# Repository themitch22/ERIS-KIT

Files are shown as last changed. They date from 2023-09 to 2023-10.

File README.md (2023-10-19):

ERIS KIT Delta 3D Printer
=========================

ERIS PARTS ONLY KITS

Manufactured in Sept & Oct 2023. 

MITCH3D inspired the kit version.  Many folks on social media have seen the great work Mitch has done with SeeMeCNC printers.  The kit is a community project.  As such, SeeMeCNC only warranties the parts included. 

The factory ERIS KIT does not include a hotend or control board.  The controller and any other electronic parts will need to be sourced seperately.

More information to complete your printer found here:
www.mitch3d.com/eris

####

Team SeeMeCNC (:

Open Source

=========================

I will maintain this fork with additional upgrade parts for the Eris Parts Kit and additional documentation.

Recommended Upgrade BOM:
*  E3D Revo Micro 12V kit
*  BTT SKR Mini E3 V3 control board
*  Voron V0.2 Mini OLED Display Controller (designed by Timmit99)
*  2 x GDSTime 3010 12V Blower Fans
*  8 x M2 x 10mm self-tapping screws
*  8 x M3 x 8mm BHCS
*  Various JST-XH crimp connectors
*  Various Dupont crimp connectors

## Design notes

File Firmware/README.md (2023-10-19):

ERIS KIT Delta 3D Printer
=========================

Firmware setup found at mitch3d.com/eris

####

Team SeeMeCNC (:

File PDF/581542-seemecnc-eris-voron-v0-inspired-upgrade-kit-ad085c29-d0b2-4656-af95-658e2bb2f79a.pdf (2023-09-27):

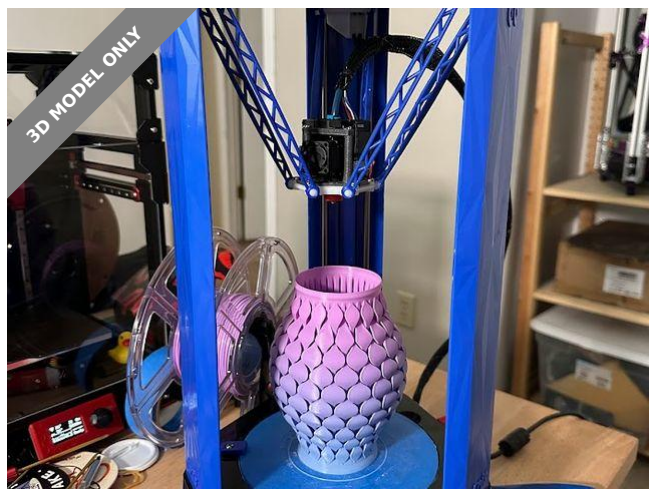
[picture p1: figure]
3D MODEL ONLY

### Summary

The ultimate upgrade package for your SeeMeCNC Eris mini delta printer (2016)

3D Printers (https://printables.com/model?categoryId=1) > Other Printer Parts & Upgrades (https://printables.com/model?categoryId=2)

Tags: raspberry | pi | eris | klipper | voron | seemecnc | v0

The SeeMeCNC Eris, (https://www.seemecnc.com/products/eris-desktop-3d-printer) released in 2016, was a ready to print out of the box mini delta printer made with injection molded parts and custom extruder hotend parts almost entirely US-made. They even sold these printers at retail stores like Microcenter!

I loved this printer, but it had some major issues:

The ATMEGA2560 based Rambo Mini board with Repetier limits a delta printers speed and precision
The HE280 based PCB on the effector used an accelerometer to detect nozzle probes for auto-calibration. It was a very advanced idea for 2016, but with modern firmware, delta-calibration techniques are way more reliable. For this mod, I have stuck with Manual Delta Calibration in Klipper and it's been super reliable for first layers.
The stock hotend and single 3010 fan was lacking. It used a bowden tube to a steel heatbreak (partially all metal) that attached the hotend to the effector PCB, the heater cartridge was a power resistor

Mitch 3D (https://printables.com/@Mitch3D)

### SeeMeCNC Eris

### Voron V0-Inspired

### Upgrade Kit

VIEW IN BROWSER (https://printables.com/model/581542-seemecnc-eris-voron-v0-inspired-upgrade-kit)

updated 13. 9. 2023 | published 13. 9. 2023

•

•

•

(about 20W), the single 3010 fan sucked air past the heatsync and it was also the part cooling with a shroud. The original print head did not have adequate heating and cooling.
The Eris had no LCD controller. It had a light up logo on front which I think was supposed to be an addressable LED, but all the control was done through MatterControl (https://www.matterhackers.com/store/l/mattercontrol/sk/MKZGTDW6) (Matterhackers) so it wasn't really portable without a PC attached.

Parts Needed and Instructions (links to vendors and files)

Original SeeMeCNC Eris - I have not found these on ebay but there are a few still floating around or collecting dust on a shelf.
BTT SKR Mini E3 V3 control board (https://biqu.equipment/products/bigtreetech-skr-mini-e3-v2-0-32-bit-control-board-for-ender-3) - It's about the same footprint as the Rambo Mini but has way more power and IO. A SKR Pico would work as well but the connectors are on the edge which might interfere with the case. You will also want an external microSD connector (https://a.co/d/5BjRwnt) pass through one of the holes and stuck to the outside of the case, this helps flash board firmware from Klipper.
SKR Mini Mounting Bracket (https://www.printables.com/model/172510-bigtreetech-skr-mini-e3-v2030-bracket) - by w0nd4bra (https://www.printables.com/@w0nd4bra) this bracket barely fits where the Rambo Mini use to slot in. I checked for clearance and marked and drilled two holes for M3x8 screws and used heat set inserts to fasten it to the shelf. You might want to use VHB tape instead. It will interfere with the corner screw bosses, you might have to sand that away. See the pictures for how I mounted it.
Raspberry Pi 3B or equivalent - These are still hard to get, you can also use the BTT Pi V1.2, the mount I designed will fit standard a Pi 3/4B, you will need to glue and heat insert the standoffs. It clips into the frame of the LCD mount backside. It provides a pass-through hole for the USB cable.
Voron V0.2 Mini OLED Display Controller (https://west3d.com/products/v0-display) (designed by Timmit99)- This controller works with Klipper with a short USB cable to the Pi (I cut the micro USB side and soldered it to a dupont connector). You will need to print the Voron V0.2 display faceplate, knob, and diffuser (https://github.com/VoronDesign/Voron-0/tree/Voron0.2r1/STLs/Display) (or hotglue like I used) using M2x10 self-tapping screws to mount into my custom Eris LCD mount. The LCD mount should slot right into the base like the original Eris logo.
E3D Revo Micro 12V kit (https://e3d-online.com/products/revo-micro) - The Revo was the smallest, lightest, easiest hotend for the Eris. The top and base mount with M3x8 screws into the plastic. The Revo wires slip through the back side cut out. I initially worked with Hotends.com to come up with a custom mount for their J-head Farmer hotend (https://hotends.com/printer-parts/hotends/j-head-farmer-hotend/) but it was too heavy. The E3D Revo comes with a 5V fan which needs a step-down converter I just soldered into the existing whip fan connections. The current design

you will need to sand down the fan shroud to not interfere

with the 3010 blowers (see picture). I would also highly
recommend using capricorn XS tube to reduce the long bowden

•

•

•

•

•

•

•

### Model files

issues like retraction, I can get away with 4mm retractions with this setup. Also check if you have the original EZstruder, you really want the latest SeeMeCNC EZR extruder (https://www.seemecnc.com/products/ezrstruder) it honestly works great as is. GDSTime 3010 12V Blower Fans (https://a.co/d/asESusC) - These part cooling fans really make a huge difference in the performance of the Eris. My effector mount base and top has M2 x 10 screw points for mounting them and a duct that blows down on to the part (I found no need for a nozzle)
I used the existing whip but removed the original connectors and soldered them to a 8-pin GX16 connector (https://a.co/d/5zVXuh1) (Use this guide for wiring) (https://hotends.com/kb/eris-3d-printer/) mounted to a hole I drilled in the case, I soldered and crimped the other side of the whip to the components on the effector side. This allows you to easily remove the whole assembly for troubleshooting and travel. You will need JST-XH crimps connectors (https://a.co/d/ebk87RT) for the BTT board and maybe some dupont 2.54 pitch connectors and crimpers.

Basically if you've build a Voron V0.1/0.2 you can handle this mod. It is basically a Voron V0 delta but not nearly as rigid or fast.

Please comment or message me and I will publish the Klipper config files needed for the Eris.
The printing results are incredible considering the age and plastic shell of this delta. It is limited to 500mm/s2 accels and 125mm/s rapids, which is quite slow for modern standards but you can't beat the portability and looks of this little printer.

If you have an Eris and want to do this mod, please message me I will try to help you with whatever I can. STEP files included if you need to modify something, I can provide Fusion 360 files if needed (they're too messy to publish).

•

•

eris-lcd-mount-pi-attachment-standoff.3mf

eris-revo-3010-effector-mount-top.3mf

### License

This work is licensed under a
Creative Commons (4.0 International License)

Attribution (http://creativecommons.org/licenses/by/4.0/)

✖ | Sharing without ATTRIBUTION
✔ | Remix Culture allowed
✔ | Commercial Use
✔ | Free Cultural Works
✔ | Meets Open Definition

eris-mini-lcd-mount.3mf

eris-lcd-mount-pi-attachment.step

eris-revo-3010-effector-mount-base.3mf

eris-mini-lcd-mount-v5.step

eris-revo-3010-effector-mount.step

eris-lcd-mount-pi-attachment-body.3mf

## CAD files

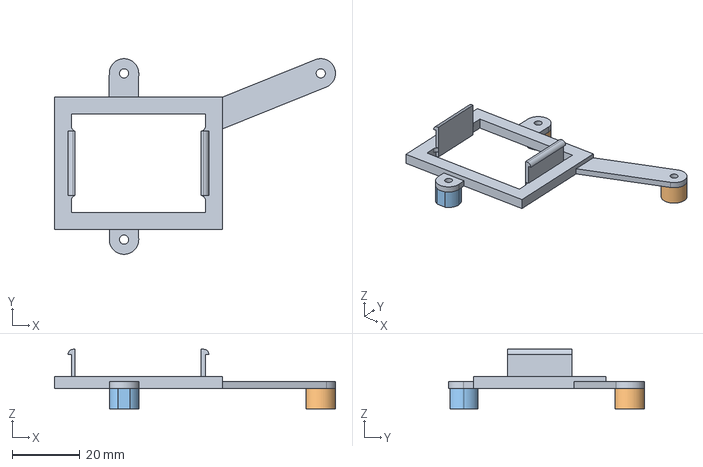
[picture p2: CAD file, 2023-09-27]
CAD/Eris LCD Mount Pi Attachment.step
82.8 x 57.7 x 17.6 mm

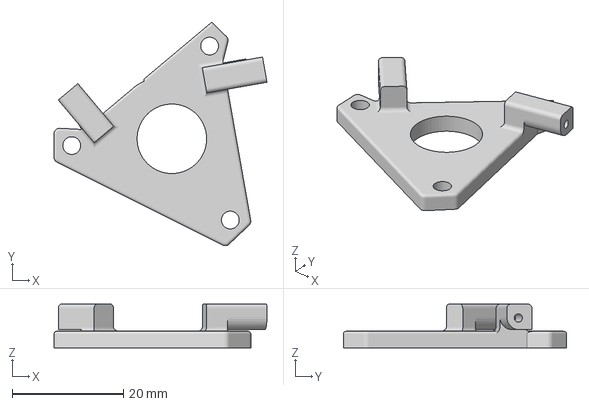
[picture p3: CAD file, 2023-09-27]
STL/Eris Revo 3010 Effector Mount Top.3mf
38.3 x 40.2 x 7.87 mm

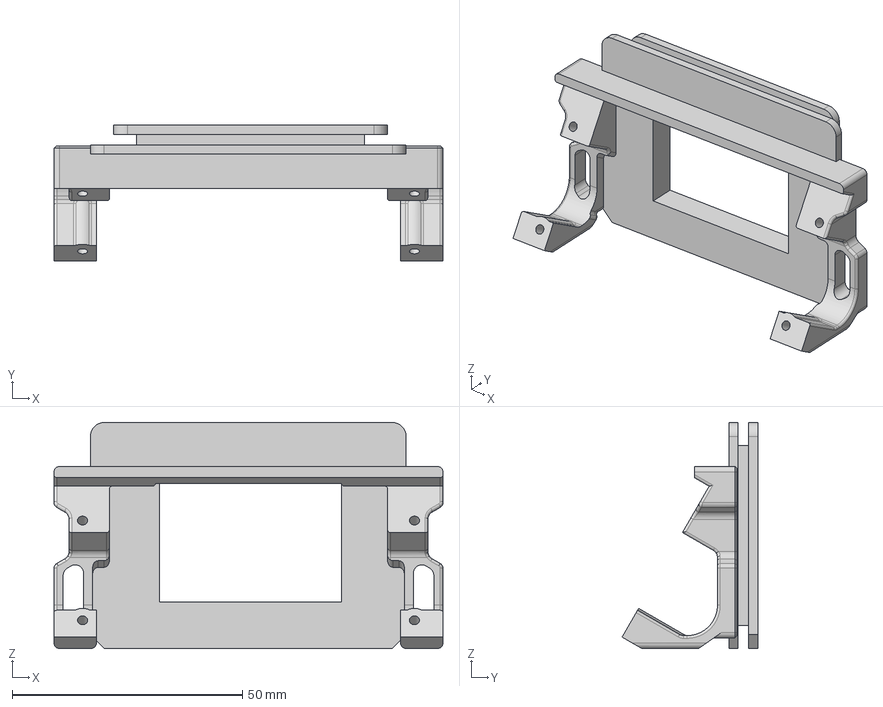
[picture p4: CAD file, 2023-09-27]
CAD/Eris Mini LCD mount v5.step
84.4 x 29.5 x 49.0 mm
Display Left Foot
Display Right Foot

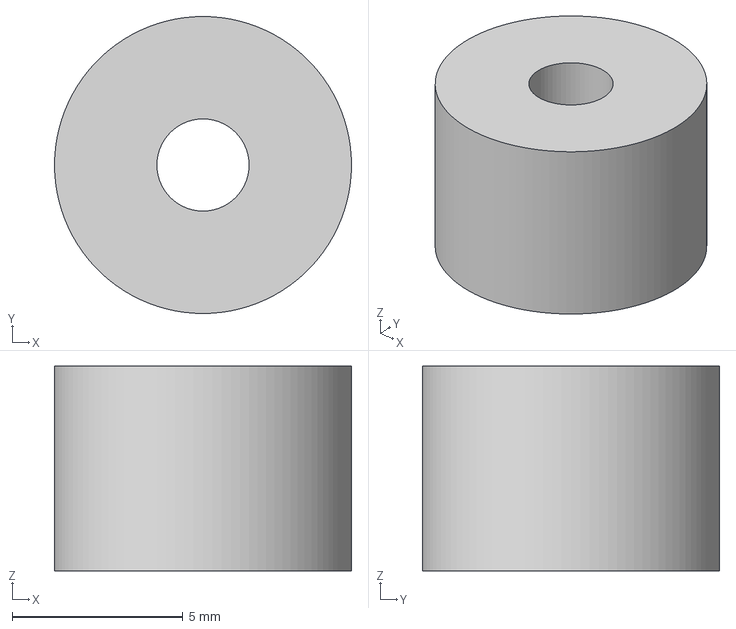
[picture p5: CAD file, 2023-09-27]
STL/Eris LCD Mount Pi Attachment Standoff.3mf
8.70 x 8.70 x 6.00 mm

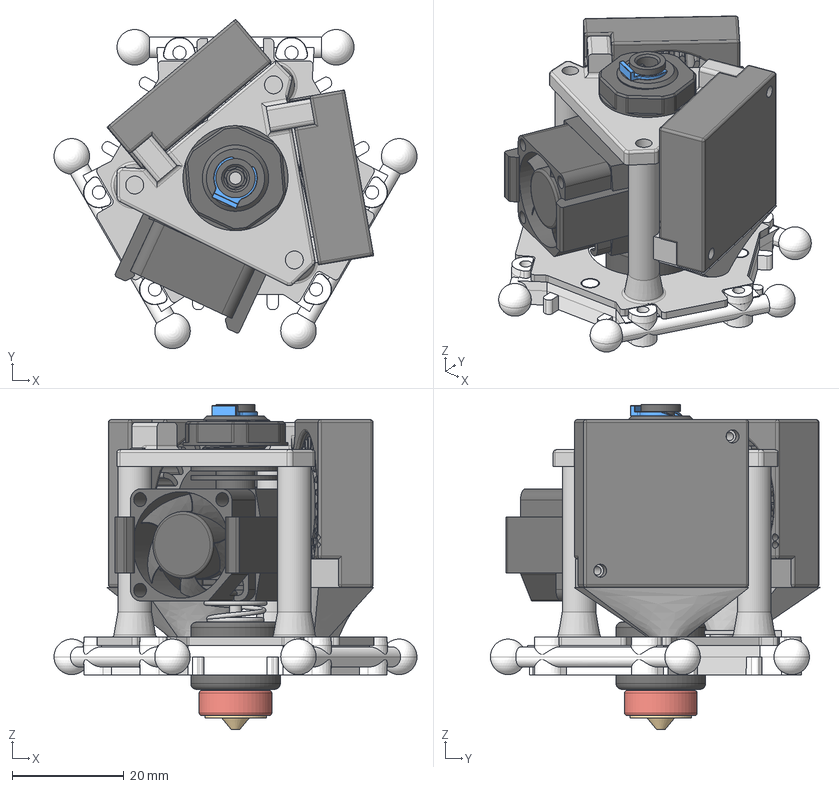
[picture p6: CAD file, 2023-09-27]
CAD/Eris Revo 3010 Effector Mount.step
64.8 x 58.8 x 58.1 mm
71200 HE280 Assembly_86005 Platform
71200 HE280 Assembly_Blower 30mm x 30mm x 10mm x 2
Heatblock
Nozzle
Threaded_Nut
Spring
Heatbreak
Heatsink
Cable_Exit
Coupling_Clip
20x20x10_Fan
Fan_Mount
Coupling

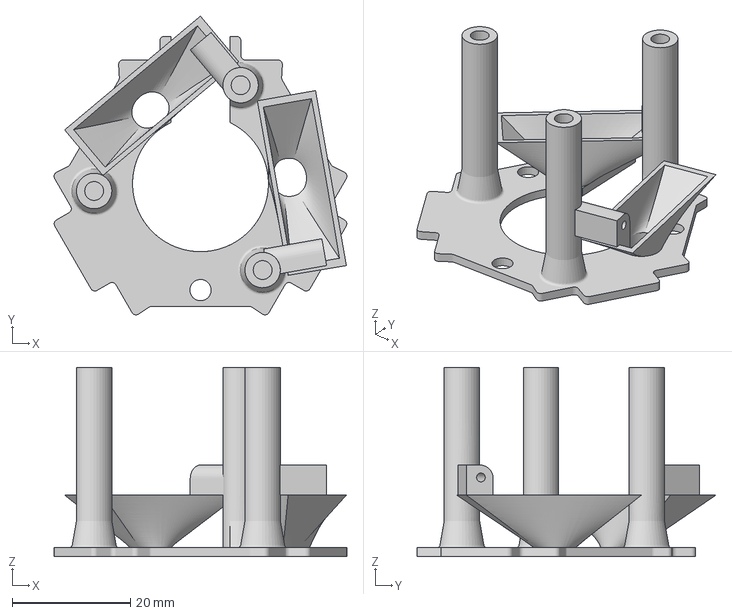
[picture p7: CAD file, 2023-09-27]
STL/Eris Revo 3010 Effector Mount Base.3mf
49.6 x 50.6 x 32.0 mm

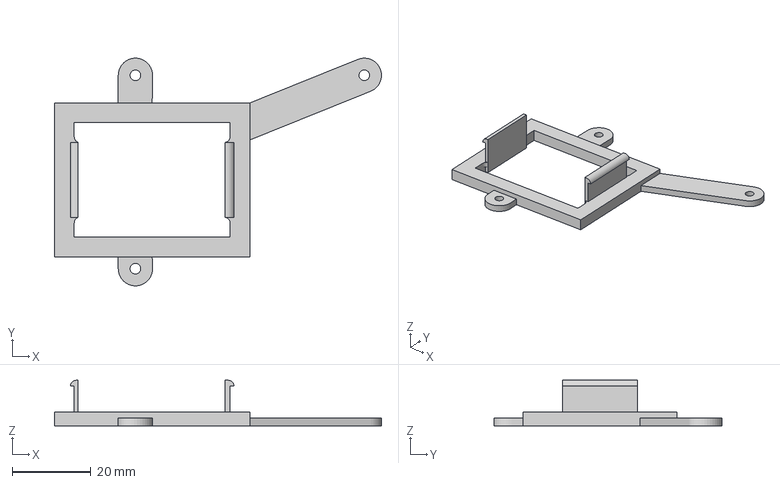
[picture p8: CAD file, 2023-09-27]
STL/Eris LCD Mount Pi Attachment Body.3mf
82.8 x 57.7 x 11.6 mm

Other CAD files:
STL/Eris Mini LCD Mount.3mf
CAD/Eris LCD Mount Pi Attachment v2.f3d
CAD/Eris Mini LCD mount v5 v1.f3d
CAD/Eris Revo Update Effector v15.f3z

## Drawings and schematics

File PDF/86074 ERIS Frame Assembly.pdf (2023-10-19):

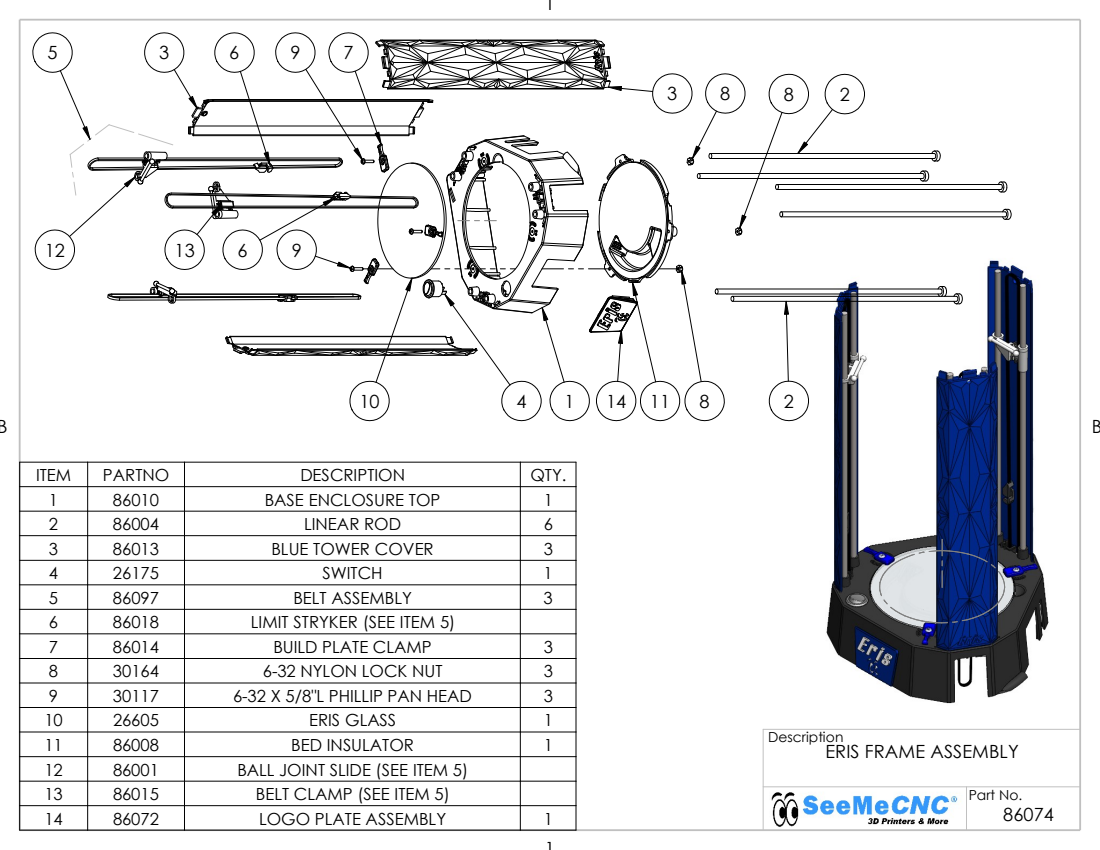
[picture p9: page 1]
BED INSULATOR

ITEM | PARTNO | DESCRIPTION | QTY.
1 | 86010 | BASE ENCLOSURE TOP | 1
2 | 86004 | LINEAR ROD | 6
3 | 86013 | BLUE TOWER COVER | 3
4 | 26175 | SWITCH | 1
5 | 86097 | BELT ASSEMBLY | 3
6 | 86018 | LIMIT STRYKER (SEE ITEM 5)
7 | 86014 | BUILD PLATE CLAMP | 3
8 | 30164 | 6-32 NYLON LOCK NUT | 3
9 | 30117 | 6-32 X 5/8"L PHILLIP PAN HEAD | 3
10 | 26605 | ERIS GLASS | 1

Description
ERIS FRAME ASSEMBLY

12 | 86001 | BALL JOINT SLIDE (SEE ITEM 5)
13 | 86015 | BELT CLAMP (SEE ITEM 5)
14 | 86072 | LOGO PLATE ASSEMBLY | 1

Part No. 86074

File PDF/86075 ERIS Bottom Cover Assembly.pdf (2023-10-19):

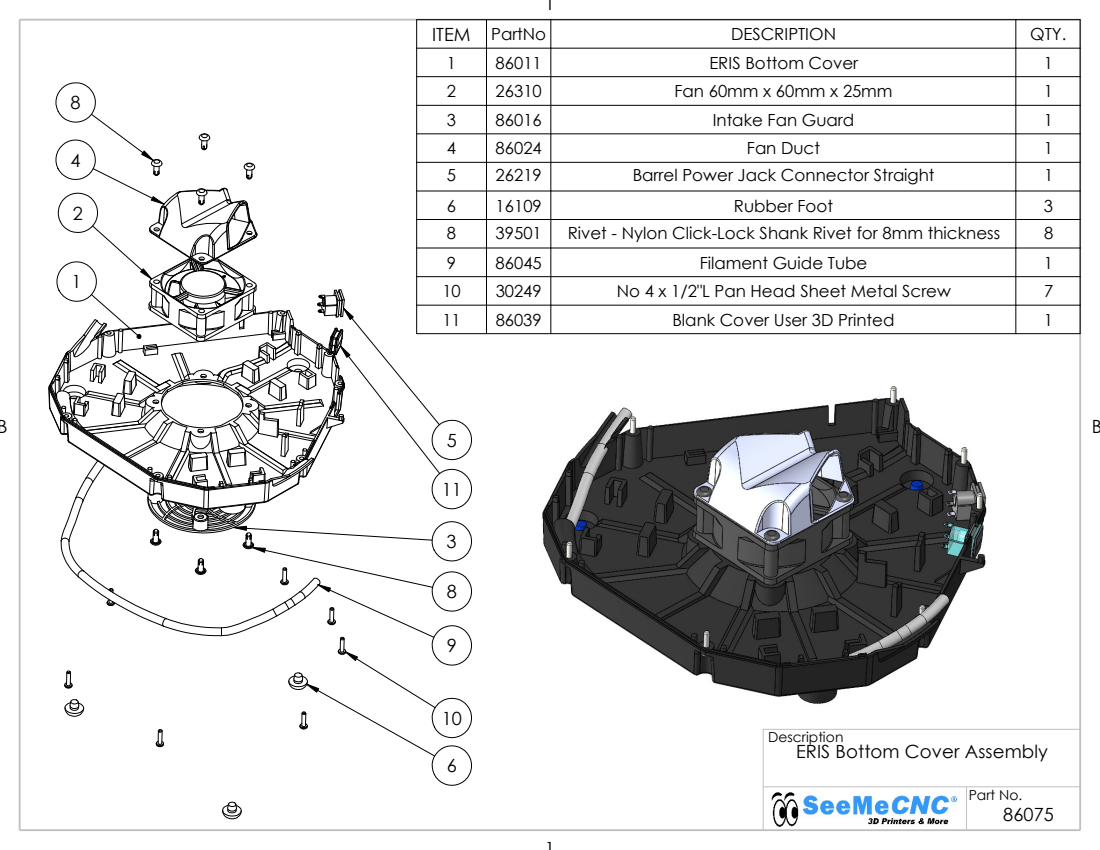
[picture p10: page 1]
Part No.

ITEM | PartNo | DESCRIPTION | QTY.
1 | 86011 | ERIS Bottom Cover | 1
2 | 26310 | Fan 60mm x 60mm x 25mm | 1
3 | 86016 | Intake Fan Guard | 1
4 | 86024 | Fan Duct | 1
5 | 26219 | Barrel Power Jack Connector Straight | 1
6 | 16109 | Rubber Foot | 3
8 | 39501 | Rivet - Nylon Click-Lock Shank Rivet for 8mm thickness | 8
9 | 86045 | Filament Guide Tube | 1
10 | 30249 | No 4 x 1/2"L Pan Head Sheet Metal Screw | 7
11 | 86039 | Blank Cover User 3D Printed | 1

Description
ERIS Bottom Cover Assembly

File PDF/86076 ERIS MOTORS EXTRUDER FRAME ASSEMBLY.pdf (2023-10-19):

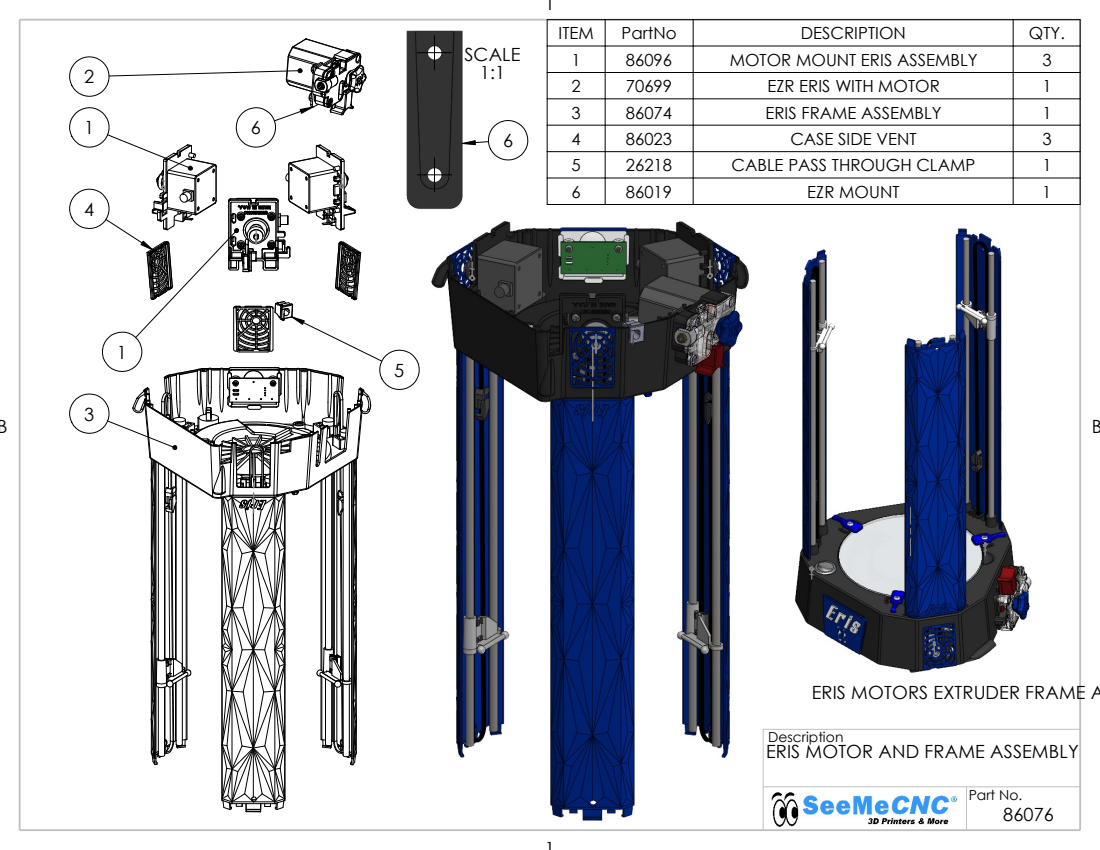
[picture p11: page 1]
Part No.; SCALE 2 1:1; ITEM; PartNo; DESCRIPTION; QTY.; MOTOR MOUNT ERIS ASSEMBLY; EZR ERIS WITH MOTOR; ERIS FRAME ASSEMBLY; CASE SIDE VENT; CABLE PASS THROUGH CLAMP; EZR MOUNT

ERIS MOTORS EXTRUDER FRAME ASSY.

Description
ERIS MOTOR AND FRAME ASSEMBLY

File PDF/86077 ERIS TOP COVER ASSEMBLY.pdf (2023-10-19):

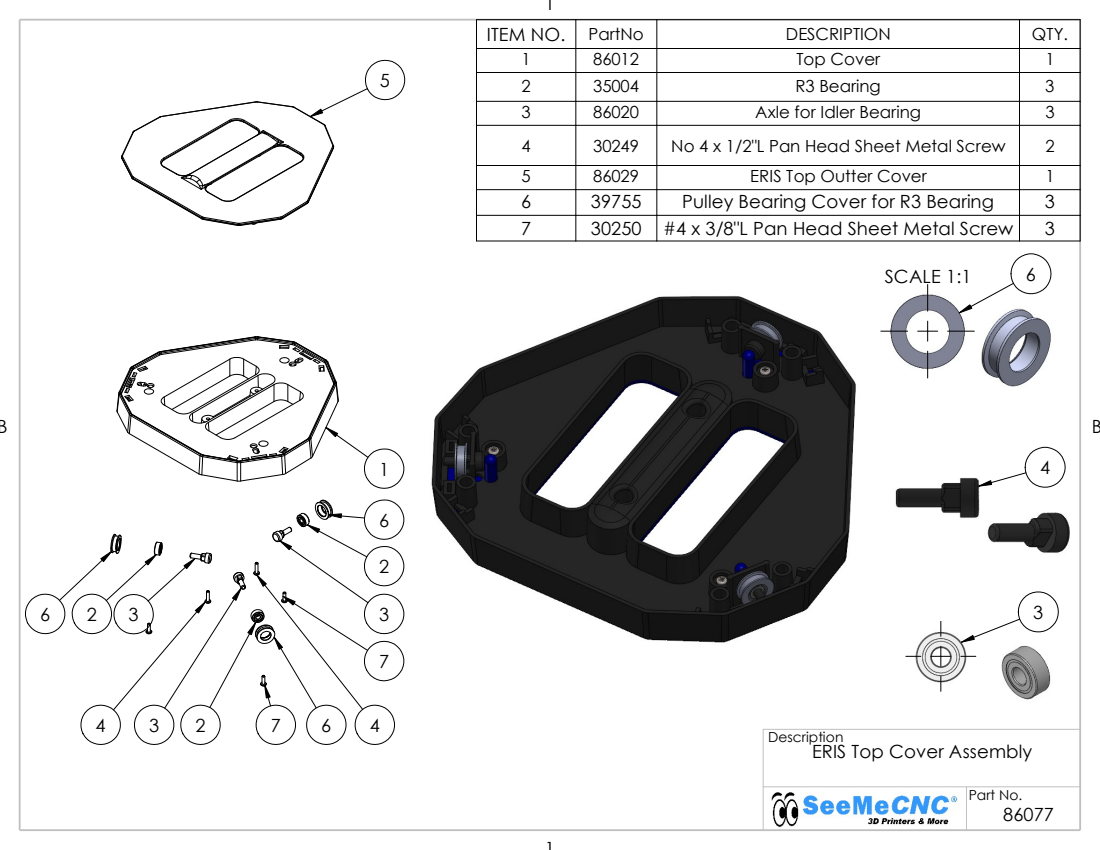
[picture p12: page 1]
Part No.; SCALE 1:1

ITEM NO. | PartNo | DESCRIPTION | QTY.
1 | 86012 | Top Cover | 1
2 | 35004 | R3 Bearing | 3
3 | 86020 | Axle for Idler Bearing | 3
4 | 30249 | No 4 x 1/2"L Pan Head Sheet Metal Screw | 2
5 | 86029 | ERIS Top Outter Cover | 1
6 | 39755 | Pulley Bearing Cover for R3 Bearing | 3
7 | 30250 | #4 x 3/8"L Pan Head Sheet Metal Screw | 3

Description
ERIS Top Cover Assembly

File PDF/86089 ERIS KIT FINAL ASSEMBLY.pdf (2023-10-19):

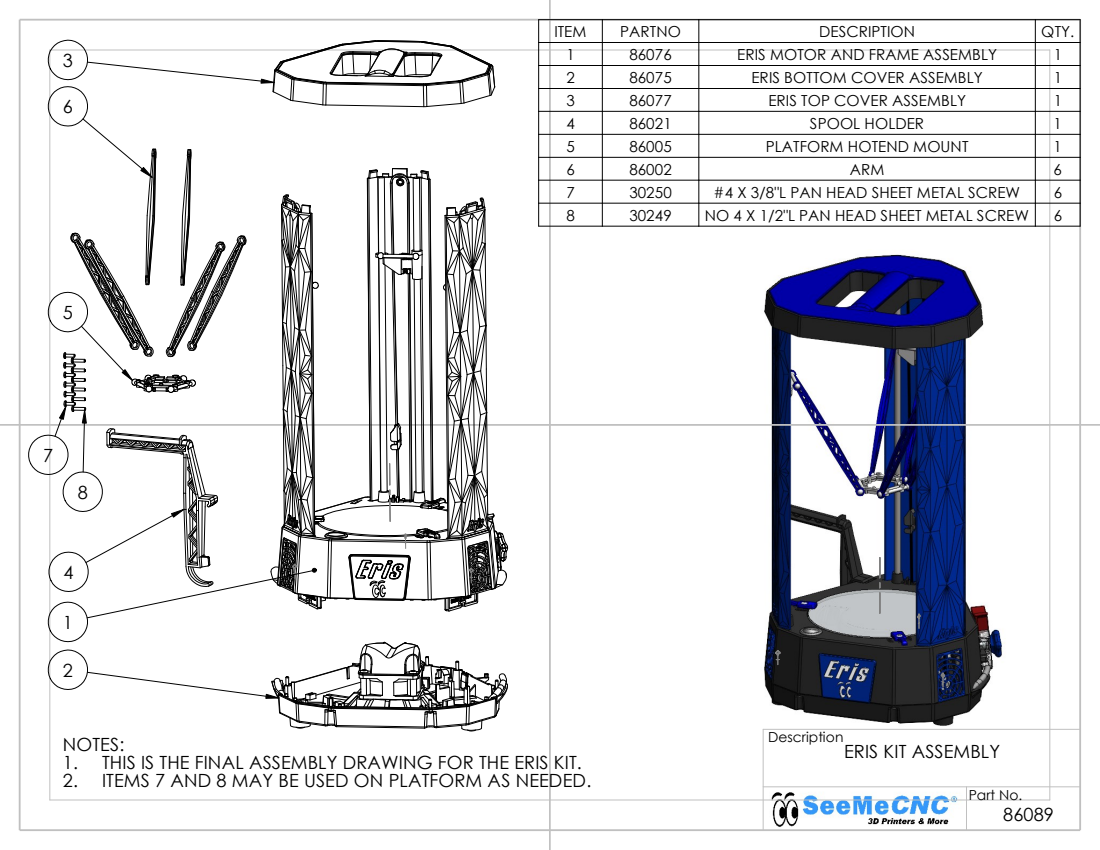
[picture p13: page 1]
ITEM; PARTNO; DESCRIPTION; QTY.; ERIS MOTOR AND FRAME ASSEMBLY; ERIS BOTTOM COVER ASSEMBLY; ERIS TOP COVER ASSEMBLY; SPOOL HOLDER; PLATFORM HOTEND MOUNT; ARM; #4 X 3/8"L PAN HEAD SHEET METAL SCREW; NO 4 X 1/2"L PAN HEAD SHEET METAL SCREW

NOTES:
1. THIS IS THE FINAL ASSEMBLY DRAWING FOR THE ERIS KIT.
2. ITEMS 7 AND 8 MAY BE USED ON PLATFORM AS NEEDED.

Description ERIS KIT ASSEMBLY

Part No.
86089

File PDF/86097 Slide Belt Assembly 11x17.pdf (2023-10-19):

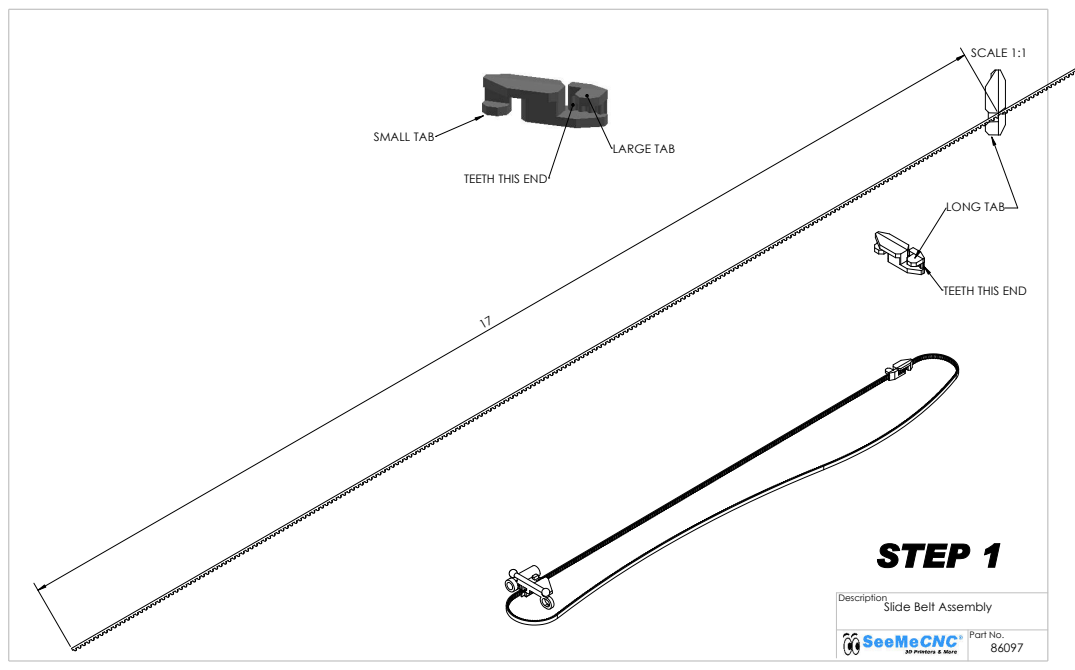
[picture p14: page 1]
Part No.; Description; LONG TAB; SMALL TAB; LARGE TAB; STEP 1; SCALE 1:1

TEETH THIS END

Slide Belt Assembly

A

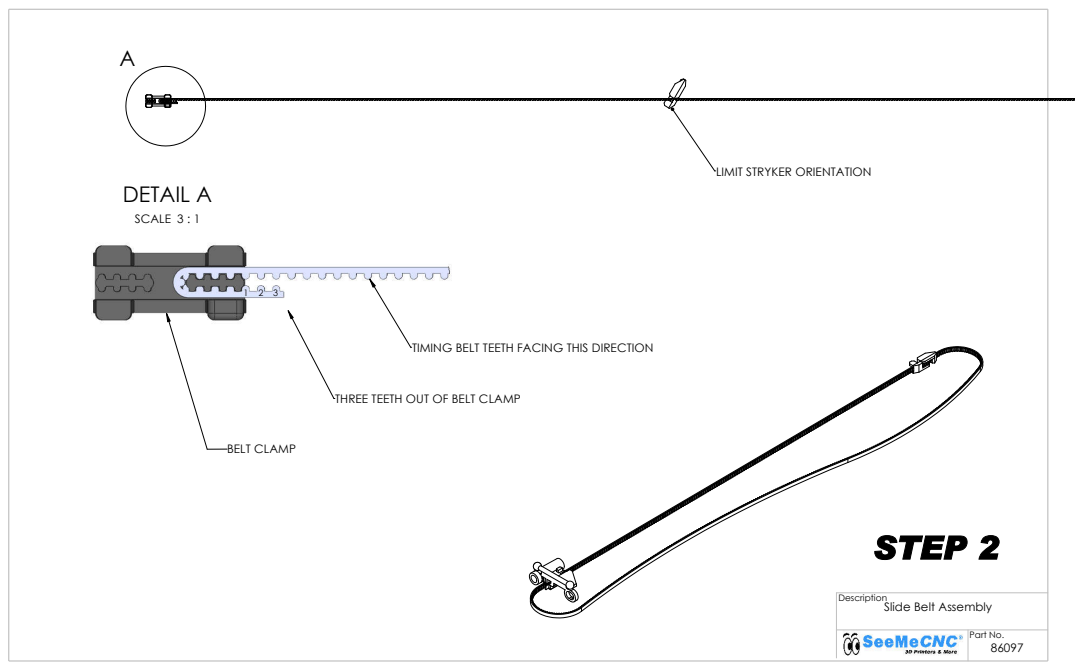
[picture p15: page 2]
Description; STEP 2; BELT CLAMP; SCALE 3 : 1; DETAIL A

LIMIT STRYKER ORIENTATION

TIMING BELT TEETH FACING THIS DIRECTION

THREE TEETH OUT OF BELT CLAMP

Slide Belt Assembly

D

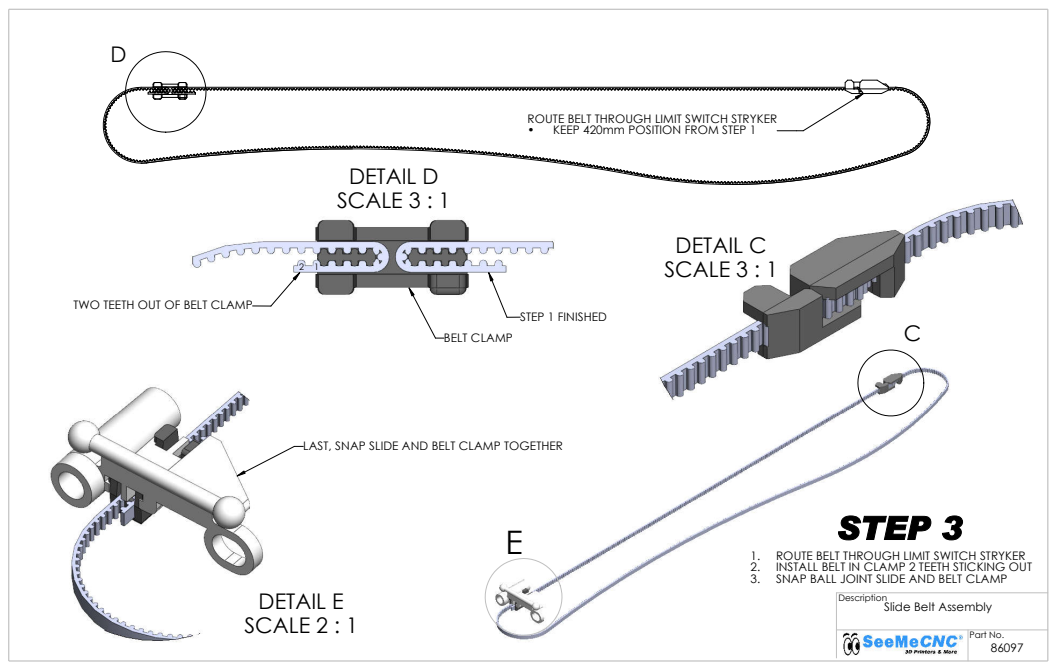
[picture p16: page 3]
Description; DETAIL C SCALE 3 : 1; ROUTE BELT THROUGH LIMIT SWITCH STRYKER; DETAIL E SCALE 2 : 1; STEP 3; SCALE 3 : 1; BELT CLAMP; STEP 1 FINISHED; DETAIL D

ROUTE BELT THROUGH LIMIT SWITCH STRYKER
• KEEP 420mm POSITION FROM STEP 1

TWO TEETH OUT OF BELT CLAMP

LAST, SNAP SLIDE AND BELT CLAMP TOGETHER

2. INSTALL BELT IN CLAMP 2 TEETH STICKING OUT
3. SNAP BALL JOINT SLIDE AND BELT CLAMP

Slide Belt Assembly

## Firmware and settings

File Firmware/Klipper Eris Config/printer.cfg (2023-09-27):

# This file is an example config file for linear delta style printers.
# One may copy and edit this file to configure a new delta printer.

# DO NOT COPY THIS FILE WITHOUT CAREFULLY READING AND UPDATING IT
# FIRST. Incorrectly configured parameters may cause damage.

# See docs/Config_Reference.md for a description of parameters.

# ================= Eris Repetier Specs ======================
#define DELTA_DIAGONAL_ROD 134.9  // 134.58 early measurement
#define DELTA_MAX_RADIUS 65  // max printable area allowed by firmware
#define PRINTER_RADIUS 98.38  //PRINTER_RADIUS-END_EFFECTOR_HORIZONTAL_OFFSET-CARRIAGE_HORIZONTAL_OFFSET
#define Z_MAX_LENGTH 175.0
#define END_EFFECTOR_HORIZONTAL_OFFSET 23.38
#define CARRIAGE_HORIZONTAL_OFFSET 10

[include mainsail.cfg]


#[include Display_macros.cfg]
#[include Display_config.cfg]
[include V0Display.cfg]
#[include menu.cfg]

[stepper_a]
step_pin: PB13
dir_pin: PB12
enable_pin: !PB14
microsteps: 16
rotation_distance: 40
endstop_pin: PC0
homing_speed: 80
#position_endstop: 190
#arm_length: 134.9

[tmc2209 stepper_a]
uart_pin: PC11
tx_pin: PC10
uart_address: 0
run_current: 0.8
#run_current: 0.580
hold_current: 0.500
stealthchop_threshold: 999999

[stepper_b]
step_pin: PB10
dir_pin: PB2
enable_pin: !PB11
microsteps: 16
rotation_distance: 40
endstop_pin: PC1
homing_speed: 80

[tmc2209 stepper_b]
uart_pin: PC11
tx_pin: PC10
uart_address: 2
run_current: 0.8
#run_current: 0.580
hold_current: 0.500
stealthchop_threshold: 999999

[stepper_c]
step_pin: PB0
dir_pin: PC5
enable_pin: !PB1
microsteps: 16
rotation_distance: 40
endstop_pin: PC2
homing_speed: 80

[tmc2209 stepper_c]
uart_pin: PC11
tx_pin: PC10
uart_address: 1
run_current: 0.8
#run_current: 0.580
hold_current: 0.500
stealthchop_threshold: 999999

[extruder]
step_pin: PB3
dir_pin: !PB4
enable_pin: !PD1
microsteps: 16
rotation_distance: 33.500
nozzle_diameter: 0.400
filament_diameter: 1.750
heater_pin: PC8
sensor_type: ATC Semitec 104NT-4-R025H42G
sensor_pin: PA0
#control: pid
#pid_Kp: 21.527
#pid_Ki: 1.063
#pid_Kd: 108.982
min_temp: 0
max_temp: 250

[tmc2209 extruder]
uart_pin: PC11
tx_pin: PC10
uart_address: 3
run_current: 0.650
hold_current: 0.500
stealthchop_threshold: 999999

[mcu]
serial: #insert USB serial ID here

[printer]
kinematics: delta
max_velocity: 100
max_accel: 500
max_z_velocity: 100
minimum_z_position=-5
#delta_radius: 65

[delta_calibrate]
radius: 50

[heater_fan extruder]
pin: PC6

[fan]
pin: PB15

[controller_fan extruder]
pin: PC7

#*# <---------------------- SAVE_CONFIG ---------------------->
#*# DO NOT EDIT THIS BLOCK OR BELOW. The contents are auto-generated.
#*#
#*# [printer]
#*# delta_radius = 64.914350
#*#
#*# [stepper_a]
#*# angle = 210.223311
#*# arm_length = 134.900000
#*# position_endstop = 188.003345
#*#
#*# [stepper_b]
#*# angle = 329.538410
#*# arm_length = 134.900000
#*# position_endstop = 185.081668
#*#
#*# [stepper_c]
#*# angle = 90.000000
#*# arm_length = 134.900000
#*# position_endstop = 186.740133
#*#
#*# [extruder]
#*# control = pid
#*# pid_kp = 34.465
#*# pid_ki = 4.995
#*# pid_kd = 59.452
#*#
#*# [delta_calibrate]
#*# height0 = 0.0
#*# height0_pos = 15041.000,14806.000,14939.000
#*# height1 = 0.0
#*# height1_pos = 17070.000,16847.000,13698.000
#*# height2 = 0.0
#*# height2_pos = 14748.000,18009.000,14641.000
#*# height3 = 0.0
#*# height3_pos = 13859.000,16485.000,16634.000
#*# height4 = 0.0
#*# height4_pos = 14689.000,14447.000,17148.000
#*# height5 = 0.0
#*# height5_pos = 16438.000,13700.000,16342.000
#*# height6 = 0.0
#*# height6_pos = 17716.000,14487.000,14608.000

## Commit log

2023-09-27 Adding Klipper config files
    [V0Display.cfg, printer.cfg]
2023-09-27 Add PDF from Printables.com page
2023-09-27 Add 3MF printable files for upgrades
    [Eris LCD Mount Pi Attachment Body.3mf, Eris LCD Mount Pi Attachment Standoff.3mf, Eris Mini LCD Mount.3mf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]
2023-09-27 Added STEP files for upgrade parts
    [Eris LCD Mount Pi Attachment.step, Eris Mini LCD mount v5.step, Eris Revo 3010 Effector Mount.step]
2023-11-07 Uploaded current Fusion 360 files
    [Eris LCD Mount Pi Attachment v2.f3d, Eris Mini LCD mount v5 v1.f3d, Eris Revo Update Effector v15.f3z]
